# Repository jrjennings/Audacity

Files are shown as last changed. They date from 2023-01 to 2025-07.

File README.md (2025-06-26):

# Audacity
## a Robo-Magellan variant of the Sawppy rover
Audacity
Goal:

+ Build a variant of the Sawppy Rover using the same basic chassis designed by Rodger Cheng<sup>1</sup> in order to compete in the Seattle Robotics Society Robo-Magellan<sup>2</sup>.

Make the following modifications to original design:

+ Change to 4 wheel drive by modifying the bogie portion of the suspension.
+ Change to gear motors with encoders for the drive motors.
+ Upgrade the steering servos to Dynamixels.

Add the following components:
+ Microcontroller: processor, memory and I/O peripherals
+ Dynamixel Shield for steering control.
+ Motor Controller to drive motors.
+ Camera for machine vision to locate orange cone.
+ Ultrasonic sensors for obstical avoidance.
+ GPS module for localization and navigation
+ 9DoF IMU for localization and navigation
+ Bumper touch sensor.
+ Tire for durability and more grip on smooth surfaces.
+ Bluetooth module to provide communication between cell phone and microcontroller.
+ 915MHz Radio for eStop fail-safe device

1. https://github.com/Roger-random/Sawppy_Rover
2. https://robothon.org/rules-robo-magellan

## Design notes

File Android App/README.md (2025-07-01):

### Created using MIT App Inventor 
### https://appinventor.mit.edu/
version 1 includes:
* bluetooth connection to rover
* remote control of steering and velocity
* wheel alignment function
*

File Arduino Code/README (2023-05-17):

version 1 includes:

bluetooth connection to rover
remote control of steering and velocity
steering alignment

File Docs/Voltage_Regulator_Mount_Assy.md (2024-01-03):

## Voltage Regulator Mount Assembly
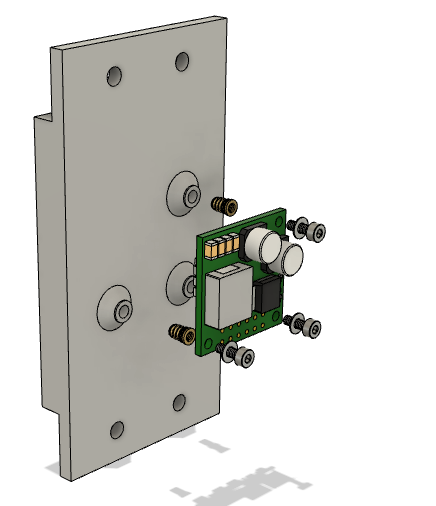
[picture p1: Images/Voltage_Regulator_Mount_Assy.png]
Voltage Regulator Mount Assembly


Parts include:
+ (1 ea) [VoltageRegulatorMount](/3d%20Prints/VoltageRegulatorMount.stl) 3D Printed (PETG)
+ (3 ea) Brass Knurled Nuts Threaded Heat Embedment for M2 screws
+ (3 ea) socket head screws M2 x 6mm - for securing Voltage Regulator to Mount
+ (3 ea) washers for M2 screws
+ (4 ea) socket head screws M3 x 8mm - for secureing Voltage Regulator Mount to Audacity Frame
+ (4 ea) washers for M3 screws

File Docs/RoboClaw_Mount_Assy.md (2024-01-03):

## RoboClaw Mount Assembly
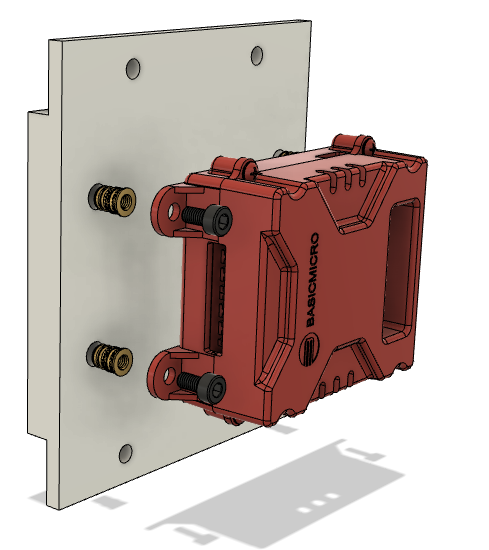
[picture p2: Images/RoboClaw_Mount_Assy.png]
RoboClaw Mount Assembly


Parts include:
+ (2 ea) [RoboClaw Mount](/3d%20Prints/RoboClaw_Mount.stl) 3D Printed (PETG)
+ (4 ea) Brass Knurled Nuts Threaded Heat Embedment for M3 screws
+ (4 ea) socket head screws M3 x 8mm - for securing RoboClaw to Mount
+ (4 ea) socket head screws M3 x 8mm - for secureing RoboClaw Mount to Audacity Frame
+ (4 ea) washers for M3 screws

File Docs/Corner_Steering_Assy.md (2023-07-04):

## Corner Steering Assembly
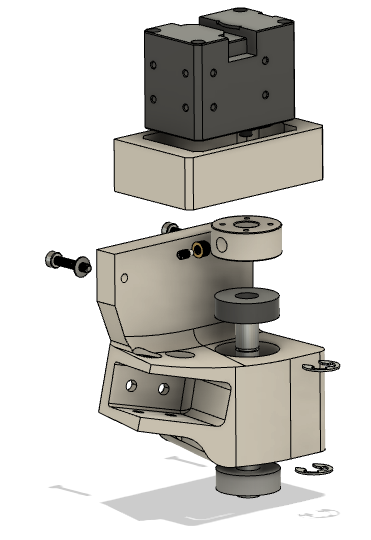
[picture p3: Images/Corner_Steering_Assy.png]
Corner Steering Assy


Pictured is an assembly view of the Corner Steering on the right front corner of the rover.

Parts include:
+ [Corner Steering Right Front](/3d%20Prints/Corner_Steering_RF_LR.stl) 3D Printed (PETG)
+ [Dynamixel Bracket](/3d%20Prints/Dynamixel%20Bracket.stl) 3D Printed (PETG)
+ [Dynamixel Coupler](/3d%20Prints/Dynamixel%20Coupler.stl) 3D Printed (PETG)
+ (1 ea) socket head screw M3 x 16mm - for securing Dynamixel Bracket to Corner Steering
+ (1 ea) washer for M3 screw
+ (4 ea) m2x5 screws that come with servo - for securing Coupler to Dynamixel

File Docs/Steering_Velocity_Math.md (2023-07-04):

## Steering Velocity Math
Pictured is the math used in the Arduino code that controls the motor speed and servo position at each corner of the rover.
Steering Velocity Math

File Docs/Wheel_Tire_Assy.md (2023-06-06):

## Wheel Tire Assembly
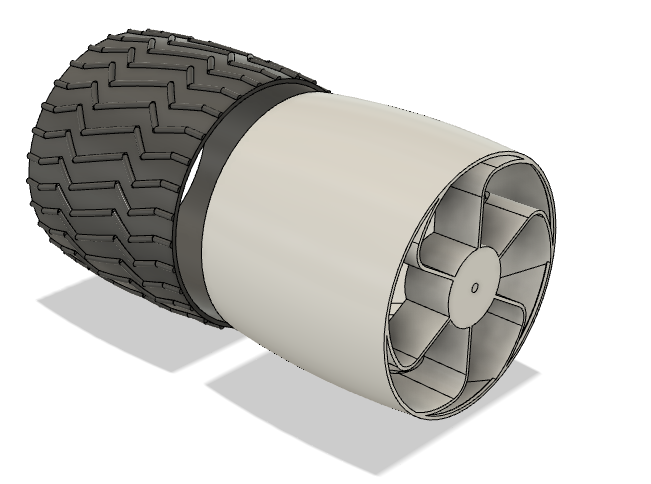
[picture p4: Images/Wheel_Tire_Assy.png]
Tire and Wheel


In order to add durability and more grip to smooth surfaces, this modification adds a TPU printed tire to a wheel that has been printed without tread.
 
 Press Tire over Wheel for snug fit.

+ [Wheel](https://github.com/jrjennings/Audacity/blob/main/3d%20Prints/Wheel_Left_R1.stl)  3D Printed (PETG)
+ [Tire](https://github.com/jrjennings/Audacity/blob/main/3d%20Prints/Tire.stl) 3D Printed (TPU)

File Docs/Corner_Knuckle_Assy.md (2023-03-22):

## Corner Knuckle Assembly
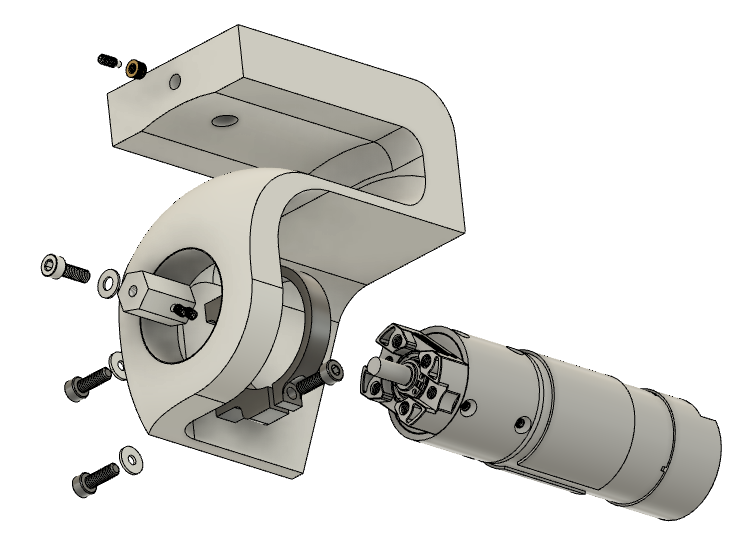
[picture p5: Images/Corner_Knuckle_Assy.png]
Corner Knuckle Assembly


Pictured is an assembly view of the Corner Knuckle on the right side of the rover.

Parts include:
+ [Corner_Knuckle](/3d%20Prints/Corner_Knuckle_Right.stl) 3D Printed (PETG)
+ Clamping Mount
+ Planetary Gear Motor
+ 12mm Hex Wheel Adapter for 6mm Motor Shaft
+ (1 ea) Brass Knurled Nuts Threaded Heat Embedment for M3 setscrew
+ (1 ea) set screws M3 x 6mm - for secureing Corner Knuckle Assy to  Corner Steering Shaft
+ (2 ea) set screws M3 x 4mm - for secureing Wheel Adapter to Motor Shaft
+ (2 ea) socket head screws M4 x 10mm - for securing Clamping Mount to Fixed Knuckle
+ (2 ea) washers for M4 screws - for securing Clamping Mount to Fixed Knuckle
+ (1 ea) socket head screw M4 x 14mm - for securing wheel to wheel adapter
+ (1 ea) washer for M4 screw - for securing wheel to wheel adapter

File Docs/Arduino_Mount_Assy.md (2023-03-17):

## Arduino Mount Assembly
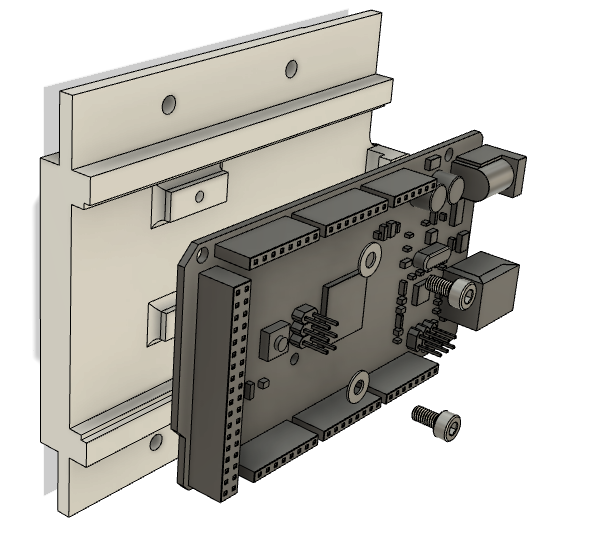
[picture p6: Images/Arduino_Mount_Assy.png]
Arduino Mount Assembly


Parts include:
+ [Arduino Mount](/3d%20Prints/Arduino_Mount.stl) 3D Printed (PETG)

+ (2 ea) socket head screws M3 x 8mm - for securing Arduino Mega to Mount
+ (2 ea) washers for M3 screws

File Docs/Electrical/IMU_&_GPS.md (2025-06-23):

## IMU and GPS 
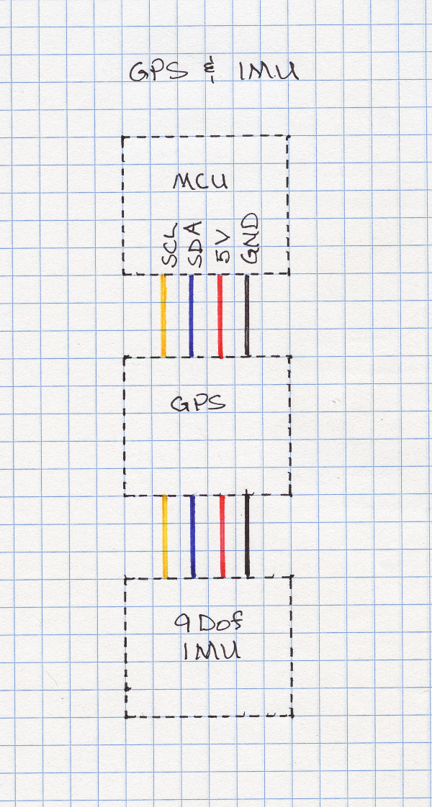
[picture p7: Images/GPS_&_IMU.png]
IMU and GPS IMU & GPS Electrical


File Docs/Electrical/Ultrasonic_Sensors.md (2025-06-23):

## Ultrasonic Sensor Array
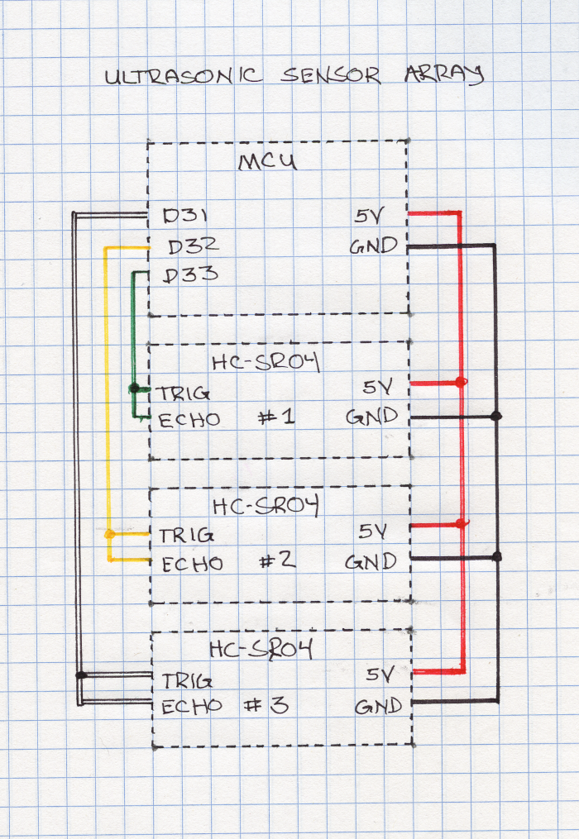
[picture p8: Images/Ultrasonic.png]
Ultrasonic Sensor Array


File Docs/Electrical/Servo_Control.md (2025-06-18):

## Steering Servo Control Electrical
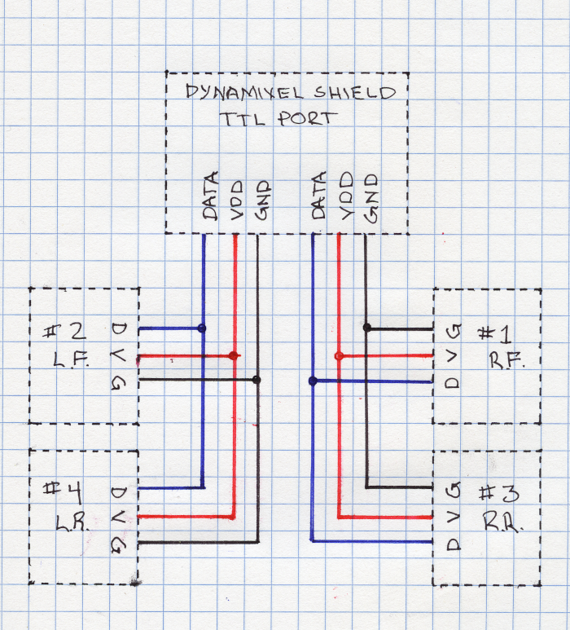
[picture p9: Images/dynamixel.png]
Servo Control Electrical


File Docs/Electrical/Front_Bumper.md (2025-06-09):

## Bumper Switch Electrical
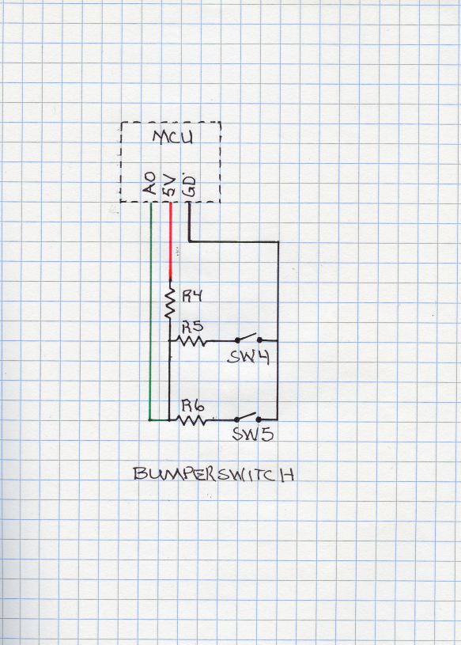
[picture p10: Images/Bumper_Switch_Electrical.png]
Bumper Switch Electrical


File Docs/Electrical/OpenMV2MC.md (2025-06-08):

## OpenMV to MicroController
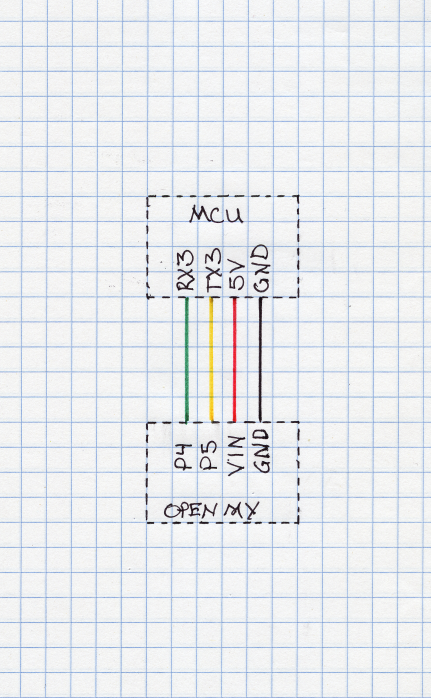
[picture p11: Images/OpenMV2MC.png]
Motor Control Electrical OpenMv to MicroController


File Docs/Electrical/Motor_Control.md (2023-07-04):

## Motor Control Electrical
Motor Control Electrical

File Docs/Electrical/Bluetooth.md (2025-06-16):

## Bluetooth Module to MCU
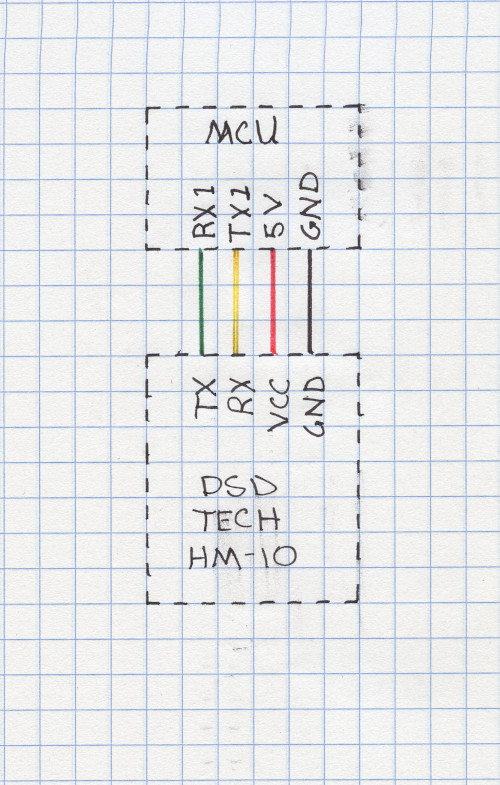
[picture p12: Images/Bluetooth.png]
Bluetooth Module to MCU


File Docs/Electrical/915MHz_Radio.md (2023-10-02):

## 915MHz Radio Electrical
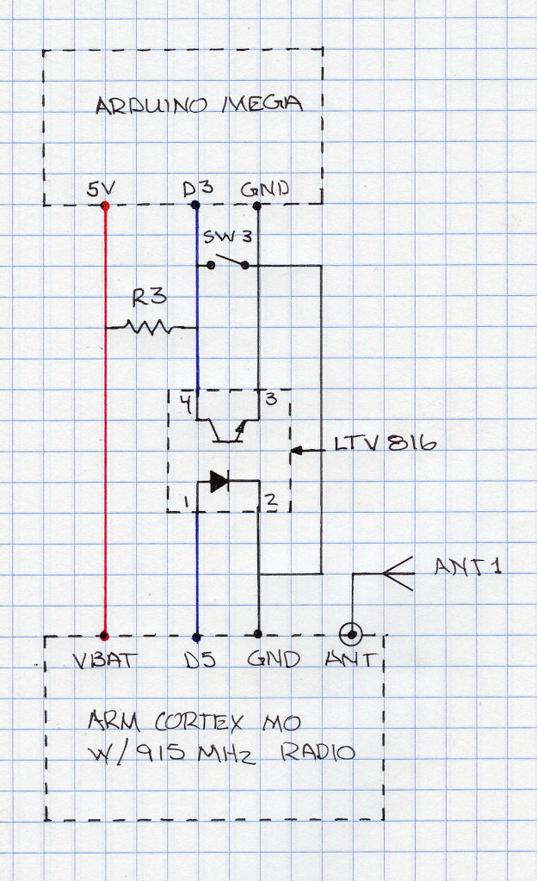
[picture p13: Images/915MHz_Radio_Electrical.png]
915MHz Radio Electrical


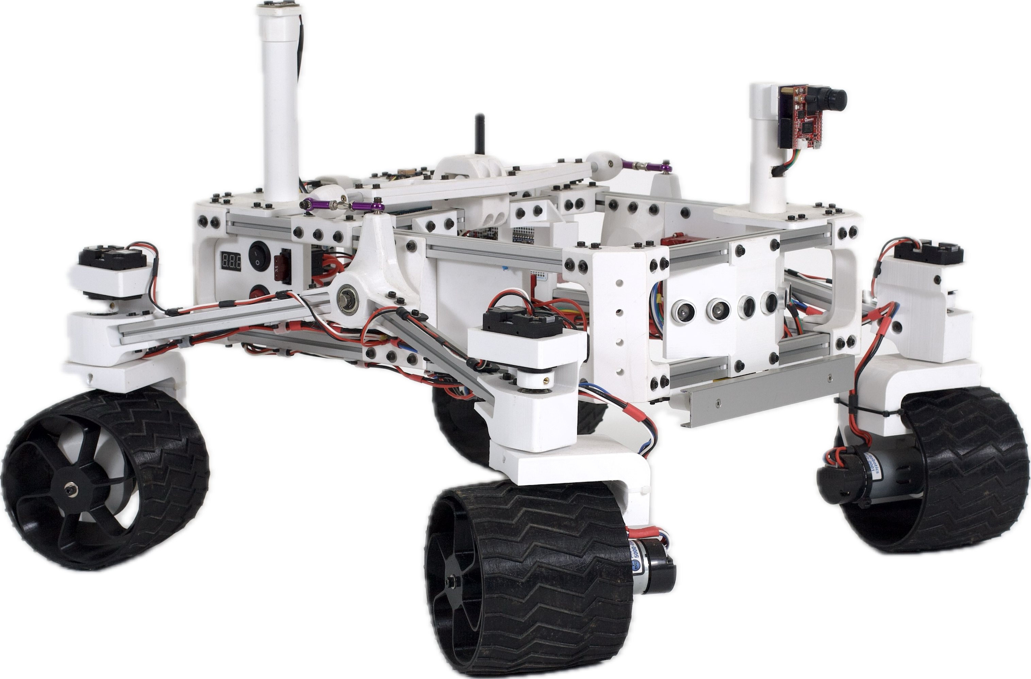
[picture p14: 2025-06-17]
Images/Audacity4.png

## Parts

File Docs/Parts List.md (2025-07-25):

# Parts List
| Quantity | Description | Vendor | Part # | Price (ea) |
| --- | --- | --- | --- | --- |
| 4 | Dynamixel | Robotis | XL430-W250-T | $49.90 |
| 1 | Dynamixel Shield | Robotis | 902-0146-000 |  $23.90 |
| 4 | 36mm Motor Clamping Mount | goBILDA | 1400-0032-0036 | $7.99 |
| 4 | Planetary Gear Motor, 223 RPM | goBILDA | 5202-2402-0027 | $42.99 |
| 2 | Roboclaw 2x7A Motor Controller | Basicmicro | IMC404 | $79.95 |
| 1 | Arduino Mega 2560 REV3 | Arduino | A000067 | $48.40 |
| 1 | 4S Lipo Battery 14.8V | Amazon | | $52.00 |
| 2 | 12mm Hex Wheel Adapter for 6mm Shaft (2-Pack) | Pololu | 2686	| $4.95 |
| 1 | DSD Tech HM-10 Bluetooth module | Amazon | | $11.49 |
| 4 | HC-SR04 Ultrasonic Sensors | Amazon|| <$3.00 |
| 1 | Mini GPS PA1010D | Adafruit | 4415 | $29.95 |
| 1 | BNO085 9DoF IMU | Adafruit | 4754 | $24.95 |
| 1 | ARM Cortex-M0 with Packet Radio 915MHz | Adafruit | 3176 | $24.95 |
| 1 | uFL SMT Antenna Connector | Adafruit | 1661 | $0.75 |
| 2 | 915MHz Antenna with uFL cable | Amazon |  | $6.99 |
| 1 | STEMMA QT/QWIIC Cable 400mm | Digi-Key | 1528-5385-ND |  |
| 1 | OpenMV H7 Plus Camera | OpenMV | | $100.00 |
| 1 | Android Phone with Operating System 2.3 "Gingerbread" or higher |
| 1 | 9V 5A Step-Down Voltage Regulator | Pololu | 4094 | $27.95 |
| 1 | Fuse Holder Blade 32V 20A PNL MNT | Digi-Key | F1888-ND | $3.60 |
| 1 | 10A Standard Blade Fuse
| 1 | DIODE SCHOTTKY 25V 10A TO220AC | Digi-Key | 497-2738-5-ND | $1.74 |
| 1 | Carbon Film Resistor 10K 1/2 watt ||||
| 2 | SPST 2 Pin 2 Position ON/Off Rocker Switch 20A/24VDC
| 1 | 4 Position Terminal Block Strip

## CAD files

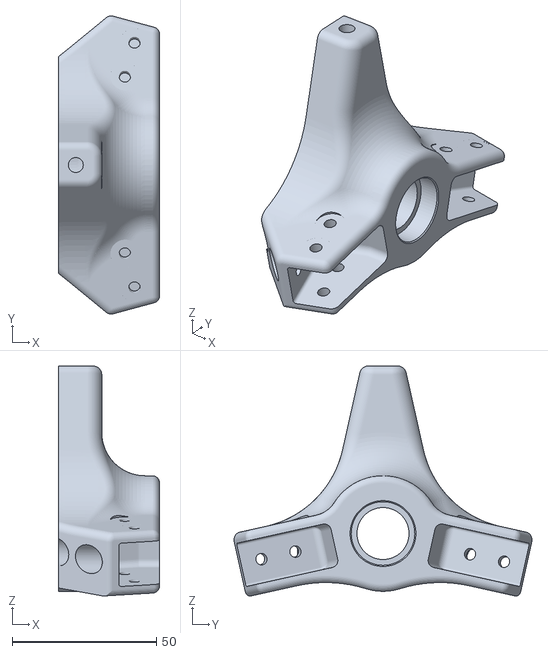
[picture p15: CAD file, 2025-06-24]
3d Prints/Rocker.stl
35.0 x 103.2 x 79.6

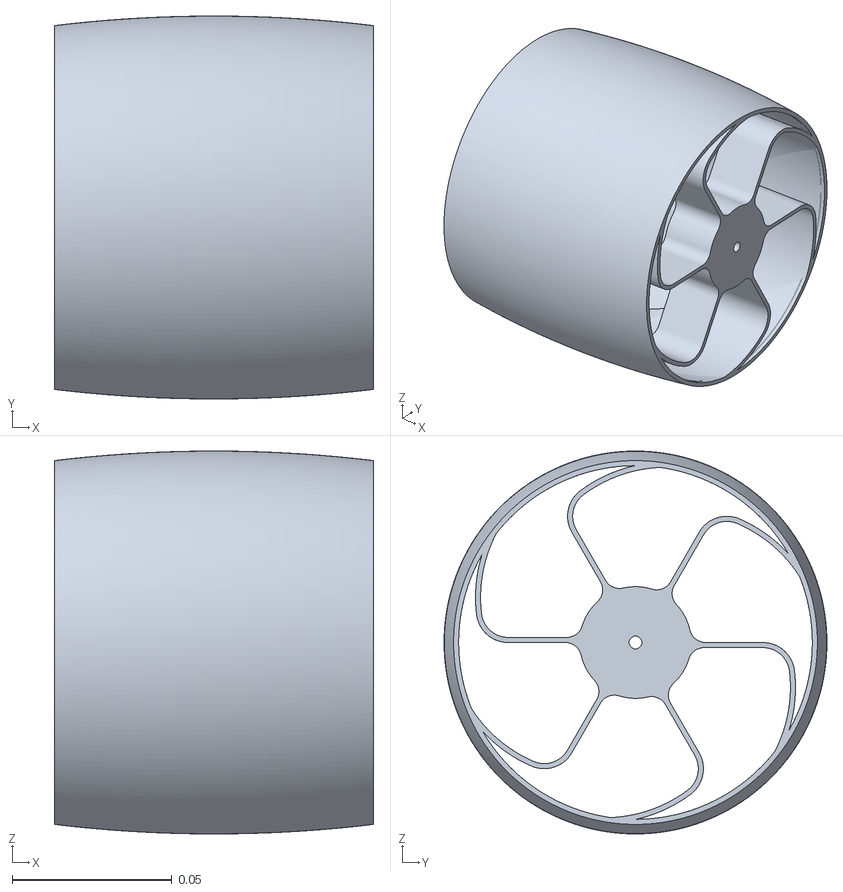
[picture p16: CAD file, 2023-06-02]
3d Prints/Wheel_Left_R1.stl
0.1 x 0.12 x 0.12

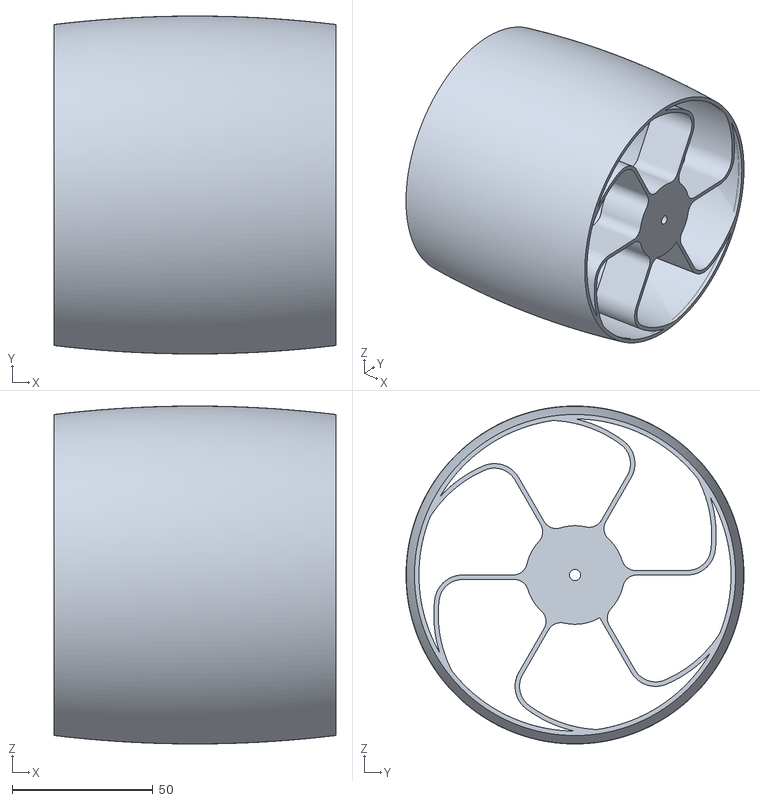
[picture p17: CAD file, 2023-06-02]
3d Prints/Wheel_Right_R1.stl
100.0 x 120.0 x 120.0

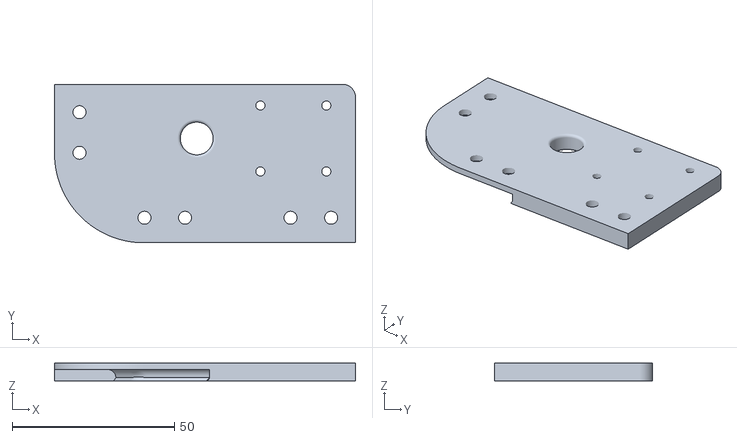
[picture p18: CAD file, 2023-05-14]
3d Prints/GPS_Mount.stl
92.7 x 48.8 x 5.50

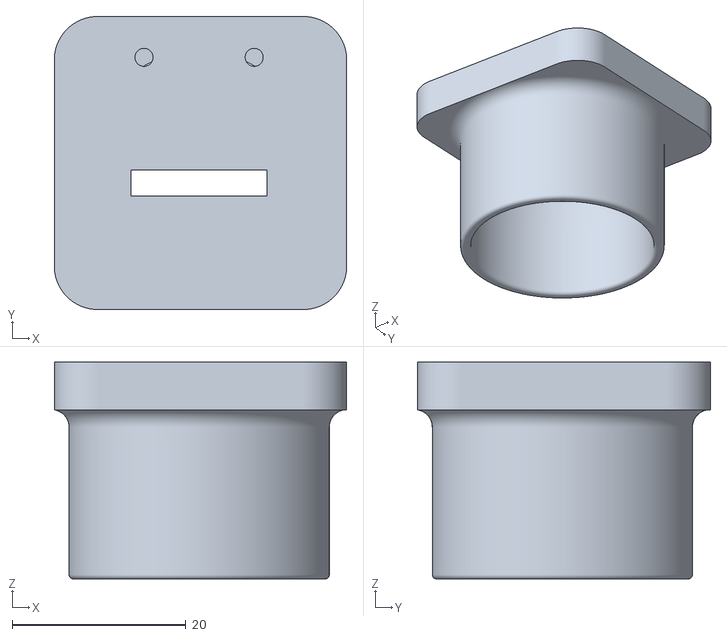
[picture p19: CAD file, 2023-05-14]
3d Prints/Magnetometer_Mount.stl
33.7 x 33.8 x 25.0

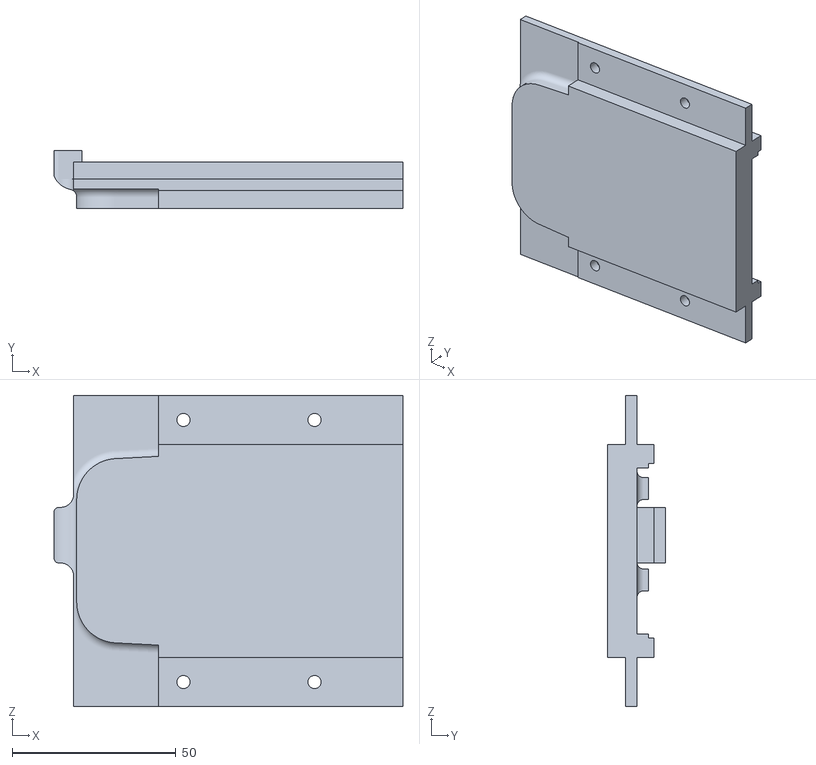
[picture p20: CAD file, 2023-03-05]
3d Prints/Arduino_Mount.stl
106.5 x 17.7 x 95.0

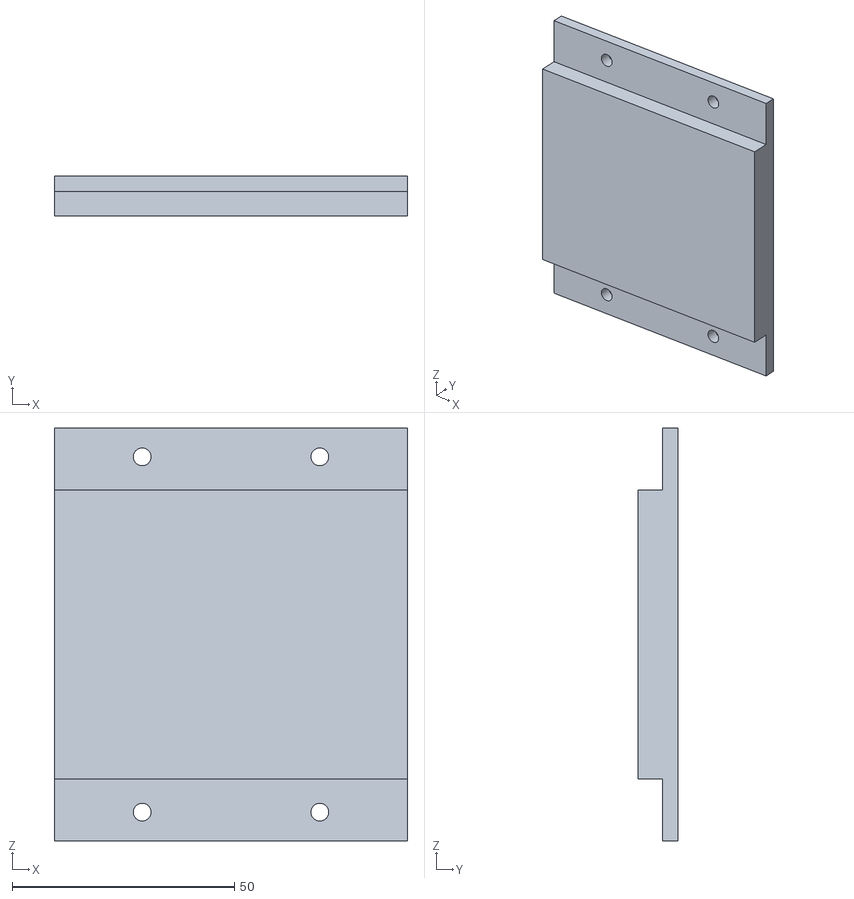
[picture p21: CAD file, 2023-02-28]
3d Prints/RoboClaw_Mount.stl
79.5 x 9.00 x 93.0

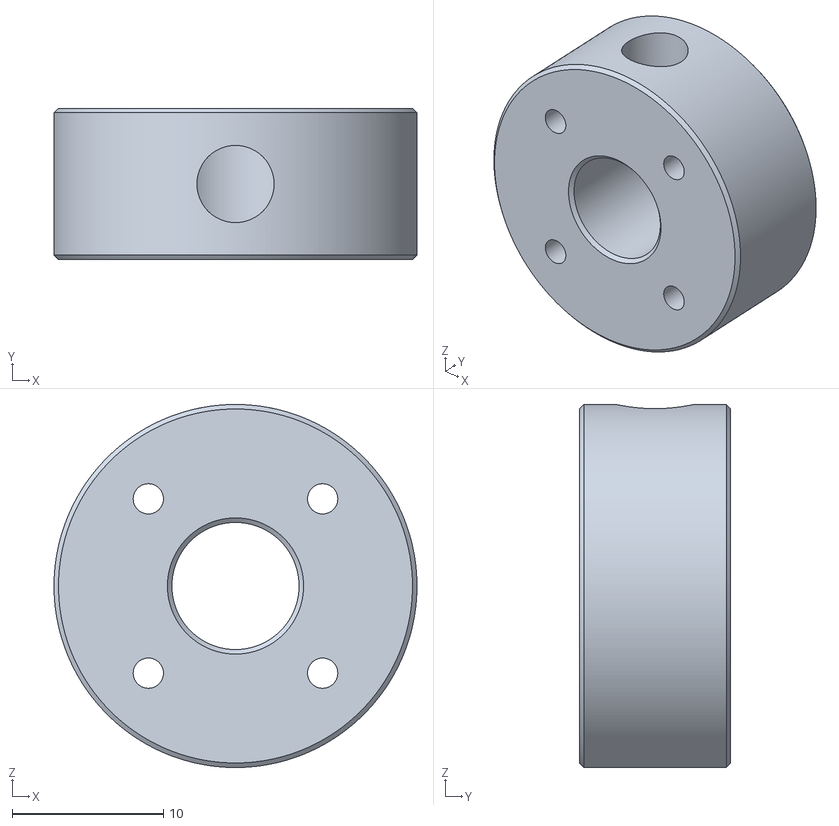
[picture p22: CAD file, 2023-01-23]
3d Prints/Dynamixel Coupler.stl
24.0 x 10.0 x 24.0

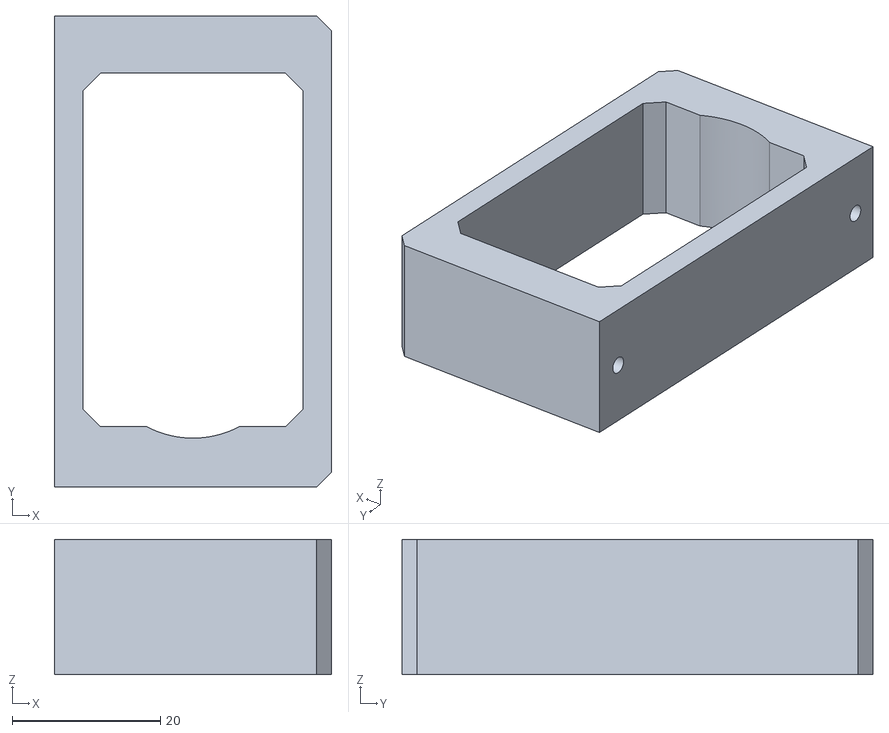
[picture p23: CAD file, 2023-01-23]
3d Prints/Dynamixel Bracket.stl
37.4 x 63.5 x 18.3

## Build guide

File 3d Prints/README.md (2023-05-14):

## directory holding all 3d print files 

### prints that modify the original design:

| Quantity | Description | Material | Notes |  |
| --- | --- | --- | --- | --- |
| 4 | Dynamixel_Bracket | PETG |||
| 4 | Dynamixel_Coupler | PETG |||
| 2 | Corner_Steering_LF_RR | PETG | Left Front & Right Rear||
| 2 | Corner_Steering_RF_LR | PETG | Right Front & Left Rear||
| 2 | Corner_Knuckle_Left | PETG |||
| 2 | Corner_Knuckle_Right | PETG |||
| 2 | Rocker | PETG |||
| 2 | Wheels_Right | PETG |||
| 2 | Wheels_Left | PETG |||
| 4 | Tires | TPU |||

### additional prints for Audacity:
| Quantity | Description | Material | Notes |  |
| --- | --- | --- | --- | --- |
| 1 | Power_Control_Panel | PETG |||
| 1 | Voltage_Regulator_Mount | PETG |||
| 1 | Termanal_Strip_Mount | PETG |||
| 1 | Arduino_Mount | PETG |||
| 1 | RoboClaw_Mount | PETG |||
| 1 | Bluetooth Module Mount | PETG |||
| 1 | Ultrasonic_Sensors_Mount | PETG |||
| 1 | OpenMV_Mount | PETG |||
| 1 | GPS_Mount | PLA |||
| 1 | Magnetometer_Mount | PLA |||
| 1 | Magnetometer_Mast_Mount | PETG |||
| 1 | Bumper_Mount | PETG |||

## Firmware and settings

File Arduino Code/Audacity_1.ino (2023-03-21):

/*AUDACITY*/
//updated 3/19/2023 

#include <DynamixelShield.h>
#include "RoboClaw.h"
#define roboClawSerial Serial1
#define bluetoothSerial Serial2
#include <Arduino.h>
RoboClaw roboclaw(&roboClawSerial,10000);

#define address1 0x80 //left side motors
#define address2 0x81 //right side motors

#include <SoftwareSerial.h>
SoftwareSerial soft_serial(7, 8); // DYNAMIXELShield UART RX/TX
#define DEBUG_SERIAL soft_serial

const uint8_t DXL_ID1 = 1;  //right front wheel
const uint8_t DXL_ID2 = 2;  //left front wheel
const uint8_t DXL_ID3 = 3;  //right rear wheel
const uint8_t DXL_ID4 = 4;  //left rear wheel
const float DXL_PROTOCOL_VERSION = 2.0;

//1 meter is = 1363 encoder counts

DynamixelShield dxl;

//This namespace is required to use Control table item names
using namespace ControlTableItem;

int s =  0; // rover speed encoder counts per second
float r = 0; // turning radius in meters
float thetaInner, thetaOuter = 0;
float speed1, speed2 = 0;

float d1 = 0.2325; // distance in meters
float d2 = 0.209;

int tab = 0;
int steering = 0;
int velocity = 0;
int triggerStateChange = 0;

//Wheel Alignment
//right front,left front, right rear, left rear
int Align[] = { -19,9,0,13};

void setup() {
  //Open Serial and roboclaw serial ports
  roboclaw.begin(38400);
  bluetoothSerial.begin(9600);  // set line end to Newline at 
  bluetoothSerial.setTimeout(50000);

  // For Uno, Nano, Mini, and Mega, use UART port of DYNAMIXEL Shield to debug.
  DEBUG_SERIAL.begin(115200);
  
  // Set Port baudrate to match with DYNAMIXEL baudrate.
  dxl.begin(1000000);
  // Set Port Protocol Version. This has to match with DYNAMIXEL protocol version.
  dxl.setPortProtocolVersion(DXL_PROTOCOL_VERSION);
  // Get DYNAMIXEL information
  dxl.ping(DXL_ID1);
  dxl.ping(DXL_ID2);
  dxl.ping(DXL_ID3);
  dxl.ping(DXL_ID4);

  // Turn off torque when configuring items in EEPROM area
  dxl.torqueOff(DXL_ID1);
  dxl.setOperatingMode(DXL_ID1, OP_POSITION);
  dxl.torqueOn(DXL_ID1);

  dxl.torqueOff(DXL_ID2);
  dxl.setOperatingMode(DXL_ID2, OP_POSITION);
  dxl.torqueOn(DXL_ID2);

  dxl.torqueOff(DXL_ID3);
  dxl.setOperatingMode(DXL_ID3, OP_POSITION);
  dxl.torqueOn(DXL_ID3);

  dxl.torqueOff(DXL_ID4);
  dxl.setOperatingMode(DXL_ID4, OP_POSITION);
  dxl.torqueOn(DXL_ID4);
}

void loop() {

  int tab;   //Tab
  int val;
  int val1;  //Steering
  int val2;  //Velocity
  int val3;  //Rotate
  int alignCorner;
  int alignmentChange;
  int triggerStateChange; 
  
  //added for BLE Versions
  if (bluetoothSerial.available() > 0){
    tab = bluetoothSerial.parseInt();   //tab4,tab3
    val1 = bluetoothSerial.parseInt();  //steering,alignCorner
    val2 = bluetoothSerial.parseInt();  //velocity,alignmentChange
    val3 = bluetoothSerial.parseInt();  //triggerStateChange,
    char r = bluetoothSerial.read();
    if(r == '\n\r'){}
  }
  else {  // if not connected to Bluetooth, rover should stop
    tab = 0;
    val1 = 0; 
    val2 = 0;  
    val3 = 0;
  }

/******************************************************************************************************
Wheel Alignment
******************************************************************************************************/
  if (tab == 3){
    // Align[Right Front, Left Front, Right Rear, Left Rear]
    alignCorner = val1;  
    alignmentChange = val2;
    triggerStateChange = val3;
    
    if ((alignCorner == 1) && (alignmentChange == 1)){  //rf
        val = Align[0] + 1;
        Align[0] = (val);
      }
    if ((alignCorner == 1) && (alignmentChange == 2)){  //rf
        val = Align[0] - 1;
        Align[0] = (val);
      }
    if ((alignCorner == 2) && (alignmentChange == 1)){  //lf
        val = Align[1]+ 1;
        Align[1] = (val);
      }
    if ((alignCorner == 2) && (alignmentChange == 2)){  //lf
        val = Align[1]- 1;
        Align[1] = (val);
      }
    if ((alignCorner == 3) && (alignmentChange == 1)){  //rr
        val = Align[2]+ 1;
        Align[2] = (val);
      }
    if ((alignCorner == 3) && (alignmentChange == 2)){  //rr
        val = Align[2] - 1;
        Align[2] = (val);
      }
    if ((alignCorner == 4) && (alignmentChange == 1)){  //lr
        val = Align[3] + 1;
        Align[3] = (val);
      }
    if ((alignCorner == 4) && (alignmentChange == 2)){  //lr
        val = Align[3] - 1;
        Align[3] = (val);
      }      
    }

/******************************************************************************************************
Remote Drive
******************************************************************************************************/
  if (tab == 4){
    steering = val1;
    velocity = val2;
    triggerStateChange = val3;
  }

/******************************************************************************************************/
  
 // int steering = val1;
  r = abs(d2 * (1/sin(steering * PI / 180))); // get length of turning radius in radians
  s = val2;

  thetaOuter = round((atan((d2 / (r + d1)))) * 180 / PI);
  thetaInner = round((atan((d2 / (r - d1)))) * 180 / PI);

  //turning right
  if (triggerStateChange == 0 && steering > 0){ 
    // Outer wheels  
    speed1 = s;
    // Inner are closer to the turing point and have lower speeds compared to the outer wheels
    speed2 = s * sqrt(pow(d2, 2) + pow((r - d1), 2)) / (r + d1);
    

    //outside left motors 2,4 speed 1
    //inside right motors 1,3 speed 2
    
    roboclaw.SpeedM1(address2,round(speed2)); // Motor 1 RF
    roboclaw.SpeedM1(address1,round(speed1)); // Motor 2 LF
    roboclaw.SpeedM2(address2,round(speed2)); // Motor 3 RR
    roboclaw.SpeedM2(address1,round(speed1)); // Motor 4 LR
    
    dxl.setGoalPosition(DXL_ID1, round(180 + thetaInner + Align[0]), UNIT_DEGREE);  //Right Front
    dxl.setGoalPosition(DXL_ID2,round(180 + thetaOuter + Align[1]), UNIT_DEGREE);   //Left Front
    dxl.setGoalPosition(DXL_ID3, round(180 - thetaInner + Align[2]), UNIT_DEGREE);  //Right Rear
    dxl.setGoalPosition(DXL_ID4,round(180 - thetaOuter + Align[3]), UNIT_DEGREE);   //Left Rear
}

  //turning left
  if (triggerStateChange == 0 && steering < 0){
    // Outer wheels 
    speed1 = s;
    // Inner front and back wheels are closer to the turing point and have lower speeds compared to the outer speeds
    speed2 = s * sqrt(pow(d2, 2) + pow((r - d1), 2)) / (r + d1);

  
    //outside right motors 1,3 speed1
    //inside left motors 2,4 speed2
    
    roboclaw.SpeedM1(address2,round(speed1));  //Motor 1 RF
    roboclaw.SpeedM1(address1,round(speed2));  //Motor 2 LF
    roboclaw.SpeedM2(address2,round(speed1));  //Motor 3 RR
    roboclaw.SpeedM2(address1,round(speed2));  //Motor 4 LR
 
    dxl.setGoalPosition(DXL_ID1,round(180 - thetaOuter + Align[0]), UNIT_DEGREE);
    dxl.setGoalPosition(DXL_ID2,round(180 - thetaInner + Align[1]), UNIT_DEGREE);
    dxl.setGoalPosition(DXL_ID3,round(180 + thetaOuter + Align[2]), UNIT_DEGREE);
    dxl.setGoalPosition(DXL_ID4,round(180 + thetaInner + Align[3]), UNIT_DEGREE);
  }

  // going straight
  if (triggerStateChange == 0 && steering == 0){
    speed1 = speed2 = s;
    
    roboclaw.SpeedM1(address2,round(speed1)); //Motor 1 RF
    roboclaw.SpeedM1(address1,round(speed1)); //Motor 2 LF
    roboclaw.SpeedM2(address2,round(speed1)); //Motor 3 RR
    roboclaw.SpeedM2(address1,round(speed1)); //Motor 4 LR
  
    dxl.setGoalPosition(DXL_ID1,180 + Align[0], UNIT_DEGREE);
    dxl.setGoalPosition(DXL_ID2,180 + Align[1], UNIT_DEGREE);
    dxl.setGoalPosition(DXL_ID3,180 + Align[2], UNIT_DEGREE);
    dxl.setGoalPosition(DXL_ID4,180 + Align[3], UNIT_DEGREE);
  }
  
  // rotate about center
  if (triggerStateChange == 1){
    speed1 = s;
    speed2 = s * 0.9291;


    roboclaw.SpeedM1(address2,round(speed1));     //Motor 1 RF
    roboclaw.SpeedM1(address1,round(speed2));     //Motor 2 LF
    roboclaw.SpeedM2(address2,round(speed1));     //Motor 3 RR
    roboclaw.SpeedM2(address1,round(speed2));     //Motor 4 LR
    

    dxl.setGoalPosition(DXL_ID1,round(129 + Align[0]), UNIT_DEGREE);
    dxl.setGoalPosition(DXL_ID2,round(231 + Align[1]), UNIT_DEGREE);
    dxl.setGoalPosition(DXL_ID3,round(227 + Align[2]), UNIT_DEGREE);
    dxl.setGoalPosition(DXL_ID4,round(137 + Align[3]), UNIT_DEGREE);
  }
}

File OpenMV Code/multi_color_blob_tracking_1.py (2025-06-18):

# This work is licensed under the MIT license.
# Copyright (c) 2013-2023 OpenMV LLC. All rights reserved.
# https://github.com/openmv/openmv/blob/master/LICENSE
#
# Multi Color Blob Tracking Example
#
# This example shows off multi color blob tracking using the OpenMV Cam.

import sensor
import time
import math

from pyb import UART

uart = UART(3, 19200, timeout_char=200)

# Color Tracking Thresholds (L Min, L Max, A Min, A Max, B Min, B Max)
# The below thresholds track in general red/green things. You may wish to tune them...
thresholds = [
    (26, 68, 36, 80, 0, 83)#,   generic_red_thresholds
    #(30, 100, -64, -8, -32, 32),  # generic_green_thresholds
    #(0, 15, 0, 40, -80, -20),
]  # generic_blue_thresholds
# You may pass up to 16 thresholds above. However, it's not really possible to segment any
# scene 3with 16 thresholds before color thresholds start to overlap heavily.

sensor.reset()
sensor.set_pixformat(sensor.RGB565)
sensor.set_framesize(sensor.QVGA)
sensor.skip_frames(time=2000)
sensor.set_auto_gain(False)  # must be turned off for color tracking
sensor.set_auto_whitebal(False)  # must be turned off for color tracking
clock = time.clock()

# Only blobs that with more pixels than "pixel_threshold" and more area than "area_threshold" are
# returned by "find_blobs" below. Change "pixels_threshold" and "area_threshold" if you change the
# camera resolution. Don't set "merge=True" because that will merge blobs which we don't want here.


def is_triangle(blob):
    # Calculate the ratio of pixels to bounding rectangle area
    rect_area = blob.w() * blob.h()
    if rect_area > 0:  # Avoid division by zero
        pixel_ratio = blob.pixels() / rect_area
        # Check if the ratio is close to 0.5 (with some tolerance)
        # You'll need to experiment to find the optimal tolerance value
        if abs(pixel_ratio - 0.5) < 0.01:  # Adjust tolerance as needed
            return True
        else:
            return False


while True:
    clock.tick()
    img = sensor.snapshot()
    blob_list = img.find_blobs(thresholds, pixels_threshold=200, area_threshold=200, feature_filter=is_triangle)
    blob_count = len(blob_list)


    for blob in blob_list:
        # These values depend on the blob not being circular - otherwise they will be shaky.
        #if blob.elongation() > 0.5:
            #img.draw_edges(blob.min_corners(), color=(255, 0, 0))
            #img.draw_line(blob.major_axis_line(), color=(0, 255, 0))
            #img.draw_line(blob.minor_axis_line(), color=(0, 0, 255))
        # These values are stable all the time.
        img.draw_rectangle(blob.rect())
        img.draw_cross(blob.cx(), blob.cy())
        # Note - the blob rotation is unique to 0-180 only.
        img.draw_keypoints(
            [(blob.cx(), blob.cy(), int(math.degrees(blob.rotation())))], size=20
        )
    #myData blob size, blob center, ratio of width to height
    myData = blob.pixels(), blob.cx()-160, round (blob.h()/ blob.w(), 1)
    if (blob_count == 1):
        stringData = str(myData)+ "\r\n"
    else:
        stringData = str("(0, 0, 0)")+ "\r\n"
    uart.write(stringData)
    time.sleep_ms(100)

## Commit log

2023-01-12 Create ArduinoMegaMount
2023-01-12 Rename 3mf/ReadMe to 3d Prints/ReadMe
2023-06-02 Add files via upload
    Revision 1 adds fillet on sprocket to hub joint
    [Wheel_Left_R1.stl, Wheel_Right_R1.stl]
